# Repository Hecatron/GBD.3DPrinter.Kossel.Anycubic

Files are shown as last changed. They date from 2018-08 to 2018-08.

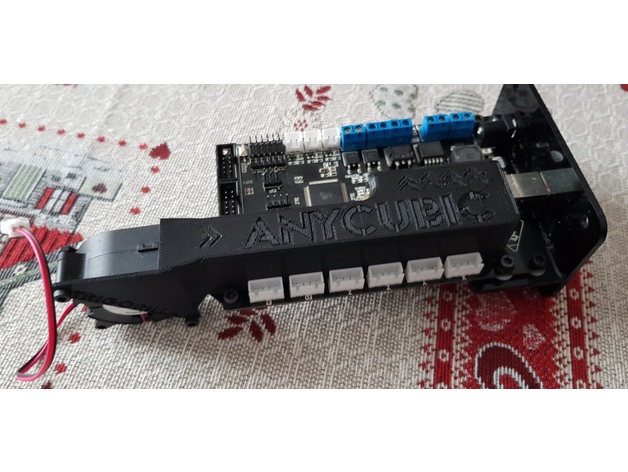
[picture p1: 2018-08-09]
Parts/Upgrades/1/Anycubic_Kossel_Essentials_Part_2_REMIX/files/Anycubic_Trigorilla_Turbo_Fan_Board_Cooler/images/2af14a65b911a9475e456cf5a4f66519_preview_featured.jpg

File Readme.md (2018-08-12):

# Readme

## TODO

Look into getting one of these displays for the Rpi

  * https://www.adafruit.com/product/3578

Also

  * https://www.thingiverse.com/thing:2859992
  * https://www.thingiverse.com/thing:2789305
  * https://www.thingiverse.com/thing:2783047

  * https://www.thingiverse.com/thing:2316500

  * https://www.thingiverse.com/thing:2024677

  * http://www.anycubic3d.com/model/show/1164.html

  * http://www.anycubic3d.com/model/show/1238.html

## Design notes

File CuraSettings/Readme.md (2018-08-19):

# Readme

Backup of settings for my Anycubic Linear Kossel Plus

Typically these settings live under
```
C:\Users\ric\AppData\Roaming\cura\3.4
```

  * Marlin-Cura-3.4 - settings I used with the original marlin / trigorilla control board
  * Duet-Cura-3.4 - settings I used for the new duet wifi control board

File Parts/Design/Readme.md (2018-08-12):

# Readme

Original frame design based on

  * https://www.thingiverse.com/thing:2965780

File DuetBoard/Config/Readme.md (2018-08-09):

# Duet Board Configuration

## Overview

  * https://configurator.reprapfirmware.org/
  * https://betrue3d.dk/duet-wifi-generating-firmware-using-configurator/

## Board Configuration Files

  * config.g – Primary configuration file, where the core configs are stored.

  * bed.g - autoleveling for Delta printers.
  * deployprobe.g - for deploying a probe for Delta printers – Removing this.
  * homedelta.g - homing on a Delta printers.
  * pause.g - for pausing the printer.
  * rResume.g - Resume file.
  * retractprobe.g - to retract a probe.

## Firmware Files

  * DuetWebControl.bin – Web Interface firmware file.
  * DuetWiFiServer.bin – WiFi Server firmware file.
  * iap4e.bin – Electronics firmware file.

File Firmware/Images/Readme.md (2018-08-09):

# Readme

Reference of pinout for trigorilla board

  * anycubic_i3_mega_trigorilla_board.jpg
  * https://drucktipps3d.de/forum/topic/anycubic-i3-mega-trigorilla-board-pin-belegung/

Images of different probes

  * Version1Probe.jpg (this is the one I have)
  * Version2Probe.jpg

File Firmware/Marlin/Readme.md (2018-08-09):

# Readme

## Overview

This is a custom firmware I've come up with for the Anycublic Kossel Linear Plus.
This is the one with the linear guides.

Also I'm using Version 1 of the Probe
As near as I can tell there were two different probes shipped with the Anycublic Kossel Linear Plus.
which uses the probe for autoleveling the bed.

  * Version 1 - has a Z offset of -19.00 below the extruder (this is the one I'm using)
  * Version 2 - has a Z offset of -14.90 below the extruder

It's possible to build your own firmware from the patches I've provided here.
These patches are against Marlin 1.1.8. See the docs directory for information on building the sources.

## Upgrading

### Backup existing firmware

First we want to backup the existing firmware just to be safe
```
avrdude -p atmega2560 -c stk500v2 -P /dev/ttyUSB0 -b 115200 -U flash:r:flash_backup_file.hex
avrdude -p atmega2560  -c stk500v2 -P /dev/ttyUSB0 -b 115200 -U eeprom:r:eeprom_backup_file.hex
```

### Upload new firmware

To overwrite / update the firmware to the one in this repository
see the file \bin\Gbd-Marlin-ProbeV1\Gbd-Marlin.ino.mega.hex
```
avrdude -p atmega2560  -c stk500v2 -P /dev/ttyUSB0 -b 115200 -e -U flash:w:Gbd-Marlin.ino.mega.hex
```

### Reset Settings

To reset the settings to all default settings
and to store them in EEPROM

  * Select Control -> Restore Failsafe
  * Select Control -> Store Settings

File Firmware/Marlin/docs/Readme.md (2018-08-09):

# Readme

This is a collection of code diffs / hex files and notes
I've collected in an attept to update the firmware on my Anycubic Kossel Delta Linear Plus
from the stock firmware which appears to be 1.1.0Rc8 to 1.1.8

## Diffs

### Diffs/Anycubic-1.1.0-rc8.patch

This is a list of differences between stock 1.1.0-RC8 and the Anycubic Sources.
In order to figure out what changes they made to configure it for Marlin.
Note this is from the Anycubic website, but I'm not entirley sure it's the same as the firmware that came with the device
I think the position of the Probe isn't setup so these sources may have been for the one without the probe.

There's also some code in there that's no longer needed for 1.1.8 which turns the fan on when the extruder gets hotter than 60 degrees
Marlin now has a proper way to do this via configuration

### Diffs/namsugak-1.1.8.patch

List of differences in a firmware updated to 1.1.8 by namsugak
It has some stuff in for LED's I'm not using, but I'm using this to check my own configuration settings for 1.1.8

### Diffs/Gbd-1.1.8.patch

TODO
Add in my own patched sources diff / Hex files

## Hex Files

### Bin/OriginalFirmware/

TODO

### Bin/Gbd-Marlin-Base/

TODO

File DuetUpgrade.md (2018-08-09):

# Duet Upgrade

## Controller Board

  * Duet WIFI

## Stepper Motors

  * https://duet3d.dozuki.com/Wiki/Choosing_and_connecting_stepper_motors
  * https://forum.duet3d.com/topic/103/choosing-0-9-degree-steppers
  * 0.9 degree
  * Nema 17
  * around 3A ?

## PSU

  * 24V Power Supply Needed
  * Current?

## Heater Block / Thermistor

Look into the best heater / thermistor using 24V

## Sensor

Look into 6 - 36V sensor

https://www.amazon.co.uk/Leveling-Self-Leveling-Adjustment-Inductive-Proximity/dp/B078K827XL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

## Connectors

### Original Connectors

The trigorrila board uses a combination of

  * 4pin JST-XH connectors - Stepper Motors
  * 2pin JST-XH connectors - Fans
  * 2pin header connectors - End Stops / thermistors
  * http://fi.eurorc.com/files/content_images/Buyers-Guide-OCo-aBalancer-Harness-4.jpg

The duet board uses Molex KK type connectors

  * 22-01-2045 - 4pin - Stepper Motors
  * 22-01-2035 - 3pin - End Stops
  * 22-01-2025 - 2pin - Thermistors and Fans
  * https://duet3d.dozuki.com/Wiki/Connector_and_spare_part_numbers

### Stepper Motor Connectors

The stepper motors use 6pin JST-XH connectors
The best plan is to get some leads with these on the end, then replace the header connectors with the Molex ones used by the Duet board

  * https://www.amazon.co.uk/BESTOMZ-Bipolar-Stepper-Printers-Machines/dp/B0746GJ7BR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

### Fan Connectors

  * https://www.amazon.co.uk/dp/B01GZKFML0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

### End Stop Connectors

TODO

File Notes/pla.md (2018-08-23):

1. printing at a higher temp such as 205 doesn't give as much adhesion as 190
so it's best to print the first layer at 190, then the follow on layer at 205 for a shiny surface finish

2. a bed temp of 50 is needed to avoid warping
a higher bed temp like 70 will stick more, but the lower layers won't cool quickly enough
which will result in the middle layers cooling before the lower ones
and a major warpage

3. general overrides

initial layer speed 5
printing temperature initial layer 190
initial layer height 0.1

4. with pla generally more fan is better for finer detail
however it can reduce bed adhesion so it's best to enable only after around 0.5mm or 6 layers

TODO try experimenting with 100% / 75%

5. rounded corners seem to be a big plus to avoid lifting as well on parts
although with a cooler bed at 50 it shouldn't be a problem

6. when leveling the bed / doing auto calibration
leave the bed at 60 for a long while to allow the heat to spread out / even out the bed
if a brim lifts at one corner this suggests the head is too far away at that corner

7. one technique I've found for bed adeshion is the initial layer height setting
at 0.1 the minimum this is good for calibrating the delta height of the printer
at a higher value the head is lifted up and more plastic is extruded to give a thicker initial layer
this sticks to the bed a lot better
however this seems to cause wrippling in the bottom surface layer
0.3 = default
0.2 = might be best

TODO try experimenting with 0.2 then baby step down by 0.05 to smoosh it into the bed

8. another technique to get better bed sticksion is to use a initial line width of 115%
https://www.sd3d.com/pla-settings/

In short

  * set the initial printing temp to 190 for the first layer, then something higher if wanted for the default for a shiny surface finish
  * use 0.1 for the initial layer height, avoid anything higher as it tends to cause wrippling - TODO
  * instead use 115% for the initial line width to help with adhesion, better alternative to large initial line height
  * use max 75% fan speed with 3 duct fan, and only full on after 0.5mm / 6 layers to help avoid warping
  * use a bed temp of 50 to avoid warping (this is a big one)
  * try to avoid non rounded corners in the model if warping is a problem

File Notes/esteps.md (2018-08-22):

M92 X80 Y80 Z80 E96                                  ; Set steps per mm
1. Measure 200mm, and put a bit of tape on
2. extrude 190mm
3. measure the amount left
4. e.g. 12mm left when it should be 10 means only 188mm has been extruded

(What you asked for / What you actually got) * current E-steps.
190 / 185 * 96 = 98.6 (new steps value)

M92 X80 Y80 Z80 E98.6                                  ; Set steps per mm

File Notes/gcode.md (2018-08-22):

Under the duet we're currently getting
"M205 command is not supported"
from the G-code output from cura

  * http://marlinfw.org/docs/gcode/M205.html

This seems to be a setting for the acceleration / speed etc

according to this

  * https://duet3d.dozuki.com/Wiki/G-Codes_not_implemented

we should be using M566 instead

TODO check different outputs from cura

gcode output changed from Marlin to Reprap
check if this works

also
https://github.com/fieldOfView/ZOffsetPlugin

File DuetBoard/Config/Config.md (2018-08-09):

# Config

## General

### General Preferences

  * Board:  Duet 2 WIFI (default)
  * Firmware version: 1.21 or newer (default)
  * Firmware compatibility: Marlin
  * Enable non-volatile memory: unchecked
    I think this isnt needed since settings are read from the sd card on startup anyway
    so we dont need g-codes loaded from the eeprom
  * Save print state on power failure: ticked
  * Auto save threshold: 10 Volts (if the psu drops below this voltage)
  * Resume threshold: 11 Volts

### Printer Geometry

  * Delta Geometry
  * Printable radius: 116.0 mm
  * Minimum Z: 0 mm
  * Diagonal rod length: 271.5 mm
  * Homed height: 295.2 mm // Auto calibrate
  * Maximum carriage travel: // I thnk not used for delta, specifed 300

  * Add a warning in config.g if you are setting your homed height too high and will measure it during calibration: ticked

#### Delta Radius

  * Smooth rod offset - 186 mm
  * effector offset - 31 mm
  * carriage offset - 20.6 mm
  * radius = 186 - 31 - 20.6
  * radius: 134.4 // Auto calibrate

## Motors

### Axes

  * Direction: Forwards - TODO test
  * Microstepping: x16 interpolate
  * Max. instant speed change: 5
    This is the jerk speed under marlin
  * Max speed: 200
  * Acceleration: 2000
  * Motor current: 1200
    motor is nema17 / 40mm deep, typically these are rated at 1.5A, so 85% of that is approx 1.2A
    The figure you put in config.g is the peak current per phase

#### Steps per mm

  * Full steps per rotation: 200
  * Belt pitch: 2
  * Pulley teeth: 20
  * Motor Steps per mm: 200 * 16 / 2 / 20
  * Motor Steps per mm: 80

### Extruders

  * Number of extruders: 1

  * Direction: Forwards - TODO test
  * Microstepping: x16 interpolate
  * Max. instant speed change: 5
  * Max speed: 50
  * Acceleration: 2000
  * Motor current: 1200

#### Steps per mm

  * Motor Steps per mm: 96
    (originally 96 in marlin)

### Motor current reduction

  * Reduce motor currents automatically when idle: ticked (default)
  * Idle current percentage: 30% (default)
  * Idle timeout: 30s (default)

## Endstops

### Z-Probe

  * Probe X Offset: 0
  * Probe Y Offset: 0
  * Probing speed: 2
    TODO I think marlin is set to 1000
  * Mode: 4
  * Deploy / retract probe (unticked)
  * Trigger Height: +16.8 // requires manual calibration
  * Trigger Value: 100 (default)
  * Recovery time: 0.4 (default)

### Endstop configuration

Endstop Type

  * X - Active High / Normally Closed
  * Y - Active High / Normally Closed
  * Z - Active High / Normally Closed

### Homing preferences

TODO

  * Homing speed (first pass): 30 (default)
  * Homing speed (second pass): 6 (default)
  * Travel speed: 100 (default)
  * Z dive height: 5 (default)

tick the box under "Set initial homing speed to 10% for calibration and add a note to homedelta.g "

## Heaters

### General heater settings

  * Number of nozel heaters: 1
  * Assign bed heater to first nozzle: unticked (default)
  * Heated bed present: ticked (default)
  * Bed heater output: Bed (default)
  * Control Method: PID // TODO selected bang bang for now
  * Chamber heater present: unticked (default)

### Heaters

For both the bed and the hotend
In marlin the thermistor setting is 5
this is labled as - 100K thermistor - ATC Semitec 104GT-2/104NT-4-R025H42G (Used in ParCan & J-Head) (4.7k pullup)
in thermistortables.h this maps to thermistortable_5.h

I think we can fine tune the B / C values using a digital thermometer

Bed

  * Temp limit: 120
  * PMW limit: 100
  * Series res: 4700 // Resistor on the controller board that is in series (correct value for duet wifi)
  * R25: 100000 // 100K at 25C temperature
  * B: 4267
  * C: 0

E0

  * Temp limit: 275
  * PMW limit: 100
  * Series res: 4700 // Resistor on the controller board that is in series (correct value for duet wifi)
  * R25: 100000 // 100K at 25C temperature
  * B: 4267
  * C: 0

## Tools

### Tool mapping

  * Number of tools: 1
  * Wait for temperatures to be reached on tool change: ticked
  * Select first tool on start-up: ticked
  * all offsets: 0mm

## Compensation

### Delta calibration

  * Number of peripheral points: 10
  * Number of halfway points: 6
  * Number of calibration factors: 7
  * Probing radius: 110

### Grid compensation

  * Probing radius: 110
  * Spacing between probe points: 25 (default)

### Orthogonal axis compensation

TODO - leave unticked for now

## Network

### Network settings 

  * Printer name: Anycubic1
  * Enable network: ticked (default)
  * Aquire dynamic IP address via DHCP: ticked (default)
  * Enable Http: ticked (default)
  * Enable FTP: unticked (default)
  * Enable Telnet: unticked (default)

  * WIFI access point name: *****
  * Password: *****
  * WIFI Password: *****

## Finish

### Cooling fans

  * Confirmed that the fans are 12V

FAN0

  * Name: Part Fan
  * Value 100%
  * Invert output: No
  * Frequency: 31Hz
  * Thermostatic Control: No

FAN1

  * Name: Hotend Fan
  * Value 100%
  * Invert output: No
  * Frequency: 31Hz
  * Thermostatic Control: Yes
  * Monitored Heaters: E0
  * Trigger temperature: 60

FAN2

  * Name: Controller Fan
  * Value 100%
  * Invert output: No
  * Frequency: 31Hz
  * Thermostatic Control: No

### Miscellaneous

  * Custom G Codes / non required

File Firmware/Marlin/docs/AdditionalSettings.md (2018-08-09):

# Additional Settings

## Overview

This is a list of changes I think are different from the original Stock firmware
That I've included in my own version of the firmware

namsugak's firmware has G26_MESH_VALIDATION disabled, I've left this enabled

## Configuration.h

### Delta AutoCalibration

Delta Auto Calibration is enabled

  #define DELTA_AUTO_CALIBRATION
  #define DELTA_CALIBRATION_RADIUS 93.0 // Default 100.8mm

### Slower feedrate for homing

The feedrate for homing has been slowed down a bit
  #define HOMING_FEEDRATE_Z  (50*60)

### Slow Probe Speed

The probing speed has been slowed down from /2 to /3
  #define Z_PROBE_SPEED_SLOW (Z_PROBE_SPEED_FAST / 3)

### Delta Probable Radius

Delta probable radius changed from -30 to -10 
  #define DELTA_PROBEABLE_RADIUS (DELTA_PRINTABLE_RADIUS - 10)

### Unified Bed Leveling

These settings where taken from namsugak's firmware settings
  #define _PX(R,A) (R) * cos(RADIANS(A))
  #define _PY(R,A) (R) * sin(RADIANS(A))
  #define UBL_PROBE_PT_1_X _PX(DELTA_PROBEABLE_RADIUS, 0)   // Probing points for 3-Point leveling of the mesh
  #define UBL_PROBE_PT_1_Y _PY(DELTA_PROBEABLE_RADIUS, 0)
  #define UBL_PROBE_PT_2_X _PX(DELTA_PROBEABLE_RADIUS, 120)
  #define UBL_PROBE_PT_2_Y _PY(DELTA_PROBEABLE_RADIUS, 120)
  #define UBL_PROBE_PT_3_X _PX(DELTA_PROBEABLE_RADIUS, 240)
  #define UBL_PROBE_PT_3_Y _PY(DELTA_PROBEABLE_RADIUS, 240)

### Grid Max points

The default setting for this is 3, Anycubic stock uses 5, I've set it to 9
  #define GRID_MAX_POINTS_X 9

### Maximum Feedrate

THe max feedrate for the Extruder is lowered from 200 to 50
  #define DEFAULT_MAX_FEEDRATE          { 200, 200, 200, 50 }

### Fixed Probe

Indicates the probe is fixed
  #define FIX_MOUNTED_PROBE

### PID Autotune

Add PID Autotune to the LCD "Temperature" menu to run M303 and apply the result.
  #define PID_AUTOTUNE_MENU

### Print Counter

This allows pulling back information on the number of prints etc via M78
  #define PRINTCOUNTER

### Nozzel Park

Specify a position for the Nozzel parking position
  #define NOZZLE_PARK_FEATURE
  #define NOZZLE_PARK_POINT { (X_MIN_POS + 10), (Y_MAX_POS - 10), 30 }
  #define NOZZLE_PARK_Z_FEEDRATE 100     // Z axis feedrate in mm/s (not used for delta printers)

### No motion before homing

This should hopfully avoid crashes into the bed
  #define NO_MOTION_BEFORE_HOMING  // Inhibit movement until all axes have been homed

## Configuration_adv.h

### Case Fan

This should allow the use the unpopulated fan header 1
for a cooling fan for the main trigorilla board
  #define USE_CONTROLLER_FAN
  #define CONTROLLER_FAN_PIN 7

### Part Cooling Fan Kick

I've noticed when running the part cooling fan at low speeds it sometimes needs a kick to get it going
This should fix that
  #define FAN_KICKSTART_TIME 100

### Advanced Pause

This should enable the advanced pause feature
  #define ADVANCED_PAUSE_FEATURE
  #define FILAMENT_CHANGE_UNLOAD_FEEDRATE 25
  #define FILAMENT_CHANGE_LOAD_LENGTH 50
  #define ADVANCED_PAUSE_EXTRUDE_LENGTH 30
  #define PAUSE_PARK_NOZZLE_TIMEOUT 600
  #define PARK_HEAD_ON_PAUSE

### Z safe homing

I think this is safe to enable
it recommends switching on for probing / auto leveling
  #define Z_SAFE_HOMING

## TODO

### Leveling Fade Height

  This seems to be disabled in one of the firmware's I've come across
  for now I'm leaving it enabled
  TODO try measuring the height of a part, if it's too high / large then try disabling

  #define ENABLE_LEVELING_FADE_HEIGHT

### Alternative auto leveling

UBL Bed leveling seems to have more features and is more detailed
but I think it has issues on non square beds, in that sense Bilinear seems to be more reliable at least with 1.1.8

I need to retry AUTO_BED_LEVELING_UBL with 1.1.x bugfix branch which has more fixes

### software endstops

try enabling this
MIN_SOFTWARE_ENDSTOPS
MAX_SOFTWARE_ENDSTOPS

### Probe Z-offset

this seems to have wrecked my probe

MSG_DELTA_Z_OFFSET_CALIBRATE
Probe Z-offset

G33 P-1

after May 12
before May 15

### Bed Leveling

so far G33 seems to do a pretty good job of getting the bed level
but using the spiral calibration, it looks like there's some regions towards the outside of the plate
which are raised / too close to the nozzel (high points)

these might be caused by the existing plate brackets, so some new ones may get around this

  * try enabling / setting up bi-linear autoleveling next and switch it on to see if it compensates
  * try replacing the bed brackets with some different ones (needs to account for the ultrabase)
  * when printing the spiral reduce the scale to 95%

DELTA_CALIBRATION_RADIUS set to 110mm about 6mm short of the printable radius
also the bed wasn't properly seated.

### Diagaonal Rod

We can tweak this value to alter the scale of the print

  * The larger this value, the smaller in scale the part becomes
  * The smaller this value, the larger in scale the part becomes

### EStep Tuning

Remember to tune the E Steps for the amount of filament extruded
(tape on filament, measure out 50mm etc)

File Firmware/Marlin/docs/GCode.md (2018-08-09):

# G-Code Commands

## Firmware Info

To get the current version of the firmware use the command M115

The output of the default firmware included with the printer is
```
FIRMWARE_NAME:Marlin 1.1.0Anycubic SOURCE_CODE_URL: PROTOCOL_VERSION:1.0 MACHINE_TYPE:Anycubic EXTRUDER_COUNT:1 UUID:cede2a2f-41a2-4748-9b12-c55c62f367ff
```

## Get Autoleveling settings

### Zero Bed

Select Measure Zero Pos seems to run the following commands

  * G36 - shortcut to the below commands

  * G28 - Auto Home
  * G29 - Auto Bed Leveling - http://marlinfw.org/docs/gcode/G029-abl.html
  * G28 - Auto Home
  * M888 - Check bed Leveling? - seems to reset the printer

### Level Bed

  * G35 - shortcut to the below commands

  * G28 - Auto Home
  * G29 - Auto Bed Leveling - http://marlinfw.org/docs/gcode/G029-abl.html
  * G28 - Auto Home
  * G30 - Do a single Z probe at a specified position. By default probe in the current position.

### General List

  * G28 - Auto Home
  * G29 - Auto Bed Leveling - http://marlinfw.org/docs/gcode/G029-abl.html
  * G30 - Do a single Z probe at a specified position. By default probe in the current position.
  * M888 - reset machine?

  * M48 - This isn't on the menu, but tests the Z probe by sampling the same spot multiple times
  * M501 - I think can read the EEPROM settings

  * G33 ? delta auto calibration?
  * http://marlinfw.org/docs/features/auto_bed_leveling.html

### Probe test

  * M119 - I think we can use this to test the Z Probe (if it should be inverted)
  to invert the probe we need to change the below settings (default it true)
  Z_MIN_ENDSTOP_INVERTING
  Z_MIN_PROBE_ENDSTOP_INVERTING

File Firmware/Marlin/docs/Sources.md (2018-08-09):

# Sources

## Base Marlin Source

### Default Marlin

 we can download the default marlin firmware for 1.1.8 - Dec 25, 2017 from here
 (unconfigured)

  * https://github.com/MarlinFirmware/Marlin/tree/1.1.8

### Bugfix 1.1.x

The latest devel version is 1.1.x, this also has a patch in for trigorilla board support

  * https://github.com/MarlinFirmware/Marlin/pull/8367
  * https://github.com/MarlinFirmware/Marlin/tree/bugfix-1.1.x

### Arduino Libraries

We may need the following arduino libs installed

  * https://github.com/olikraus/U8glib_Arduino \\
    For a full graphics display

## Stock Firmware

  * http://www.anycubic3d.com/support/show/594034.html
  * https://www.thingiverse.com/thing:2220077

There seems to be around 3 different versions of the firmware available from the official site

  * Kossel Plus_20170712
    This seems to be a source based distro, I think the same version included with the printer Marlin 1.1.0-RC8 - 6 Dec 2016
    TODO is autoleveling enabled?
 
  * ANYCUBICkossel Auto leveling_20171113 (version 1 / version 2)
    This includes two binary based hex files (no source) also appears to be Marlin 1.1.0
    It looks like there's 2 different versions of the probe so they've included 2 versions and a picture to match against the probe
    My probe appears to be V1, I suspect the V2 probe has a different height measurement.

In order to work out what custom settings have been applied we can compare it to version 1.1.0-RC8

  * https://github.com/MarlinFirmware/Marlin/tree/1.1.0-RC8

see Diffs/Anycubic-1.1.0-rc8.patch

## Other Firmwares

### namsugak firmware

This appears to have Neopixel support and is based on 1.1.8
however it's setup for the V2 sensor, I think mine is V1

  * https://www.thingiverse.com/thing:2803527

### ArtieH firmware

This one is more recent, it's based on the 1.1.x bugfix branch
this seems to be more of a dev version

  * https://www.thingiverse.com/thing:2927795

### Another firmware

  * https://github.com/ruevs/Marlin_Anycubic_Kossel

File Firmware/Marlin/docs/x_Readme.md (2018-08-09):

# Readme

## Overview

This directory contains some hex binary files for different Marlin versions

  * **OriginalFirmware** - A backup of the version of Marlin that came with my Anycubic Kossel Linear Plus <br>
    This has version 1 of the probe as far as I can tell, and is Marlin 1.1.8RC8

  * **Gbd-Marlin-Base** - My own version of Marlin 1.1.8, no modifications other than trying to update from 1.1.0-RC8 to 1.1.8

When compiling using the Arduino Software

  * select the board Tools -> Board -> Arduino Genuino Mega or Mega 2560
  * select Verify / Compile
  * select Sketch -> Export Compiled Binary
  * the hex file (use the one without the bootloader) will be in the Marlin Source directory

## AVRDude commands

### Backup existing firmware

  * https://forum.arduino.cc/index.php?topic=403201.0

To backup the main firmware, reset the device then run
```
avrdude -p atmega2560 -c stk500v2 -P /dev/ttyUSB0 -b 115200 -U flash:r:flash_backup_file.hex
```

To backup the eeprom reset the device
make sure octoprint is disconnected
then run
```
avrdude -p atmega2560  -c stk500v2 -P /dev/ttyUSB0 -b 115200 -U eeprom:r:eeprom_backup_file.hex
```

### Write new firmware

To write a hex file
```
avrdude -p atmega2560  -c stk500v2 -P /dev/ttyUSB0 -b 115200 -e -U flash:w:flash_backup_file.hex
```

To write a backed up eeprom
```
avrdude -p atmega2560  -c stk500v2 -P /dev/ttyUSB0 -b 115200 -U eeprom:w:eeprom_backup_file.hex
```

### Hex to Bin conversion

to convert binary to hex
```
srec_cat.exe BinFile.bin -Binary -o HexFile.hex -Intel
```
to convert hex to binary
```
srec_cat.exe HexFile.hex -Intel -o BinFile.bin -Binary
```

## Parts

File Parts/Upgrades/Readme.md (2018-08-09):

# Readme

Collection of upgrades, some sourced from thingiverse <br>
for an anycubic linear plus (one with rails)

  * https://www.thingiverse.com/tag:Anycubic_Kossel_Plus/

## Custom Upgrades

### Camera Mount

A couple of parts for mounting a camera on the 3d printer - Advent AWCAMHD15

### Rpicase-Lasercut

Designs for a laser cut case for a Rpi to mount on the printer.
The printer version includes M4 mounting holes for the 20x20 extrusion

### LargeDisplayMount

Panel to mount a larger LCD display on the front of the printer <br>
KOOKYE LCD 12864 Graphic Smart Display Controller Module with Connector Adapter & Cable for RepRap RAMPS 1.4 3D Printer kit Arduino Mega 2560 R3 Shield

  * https://www.amazon.co.uk/gp/product/B019SXNH1S/

Look into

  * https://www.thingiverse.com/thing:2911892
  * https://www.thingiverse.com/thing:2489092

## Thingiverse Upgrades

### ExtruderClip

Can be used when changing filaments

  * https://www.thingiverse.com/thing:2935798

### Flexible filament holder

  * https://www.thingiverse.com/thing:2788235

### Cable Holder

  * https://www.thingiverse.com/thing:2897799

### Bottom Cover

This one has ventalation holes and mounting holes for M4 bots

  * https://www.thingiverse.com/thing:2771991

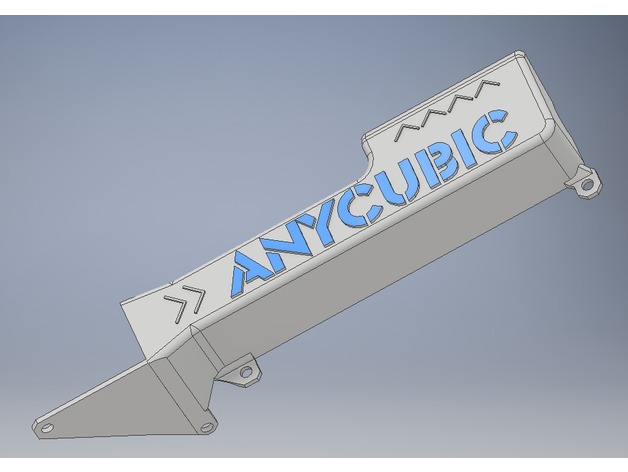
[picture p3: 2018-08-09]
Parts/Upgrades/1/Anycubic_Kossel_Essentials_Part_2_REMIX/files/Anycubic_Trigorilla_Turbo_Fan_Board_Cooler/images/becb625ca1ba965f619c9286a48681f2_preview_featured.jpg

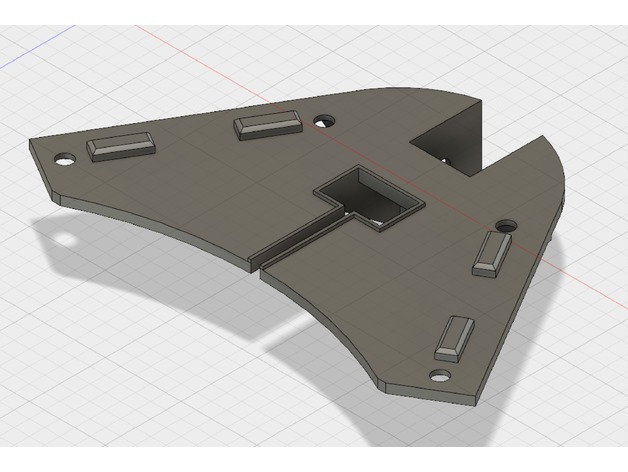
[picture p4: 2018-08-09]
Parts/Upgrades/1/Anycubic_Kossel_Essentials_Part_2_REMIX/files/Kossel_Plus_Boden_Platte_Kossel_Plus_Bottom_Plate_240mm/images/79d7a0f26c9bd90c7aafae191fd92289_preview_featured.jpg

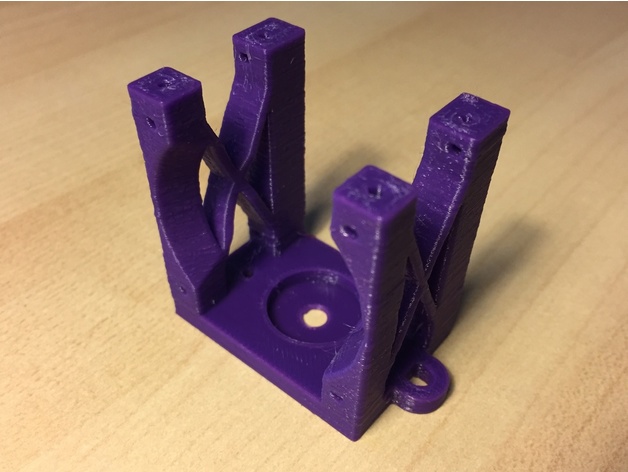
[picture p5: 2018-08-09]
Parts/Upgrades/1/Anycubic_Kossel_Essentials_Part_2_REMIX/files/Anycubic_Kossel_Hotend_Mount_Zesty_Nimble_Mount_Holes/images/835dffdc6f4afb127d733eec75e4aa49_preview_featured.JPG

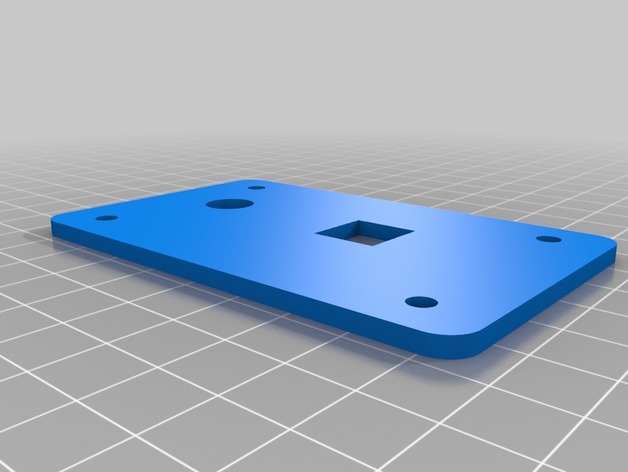
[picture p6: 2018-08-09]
Parts/Upgrades/1/Anycubic_Kossel_Essentials_Part_2_REMIX/files/Anycubic_Kossel_mainboard_cover/images/d7e54eb4350ff4413ee2c9dc20198bfc_preview_featured.jpg

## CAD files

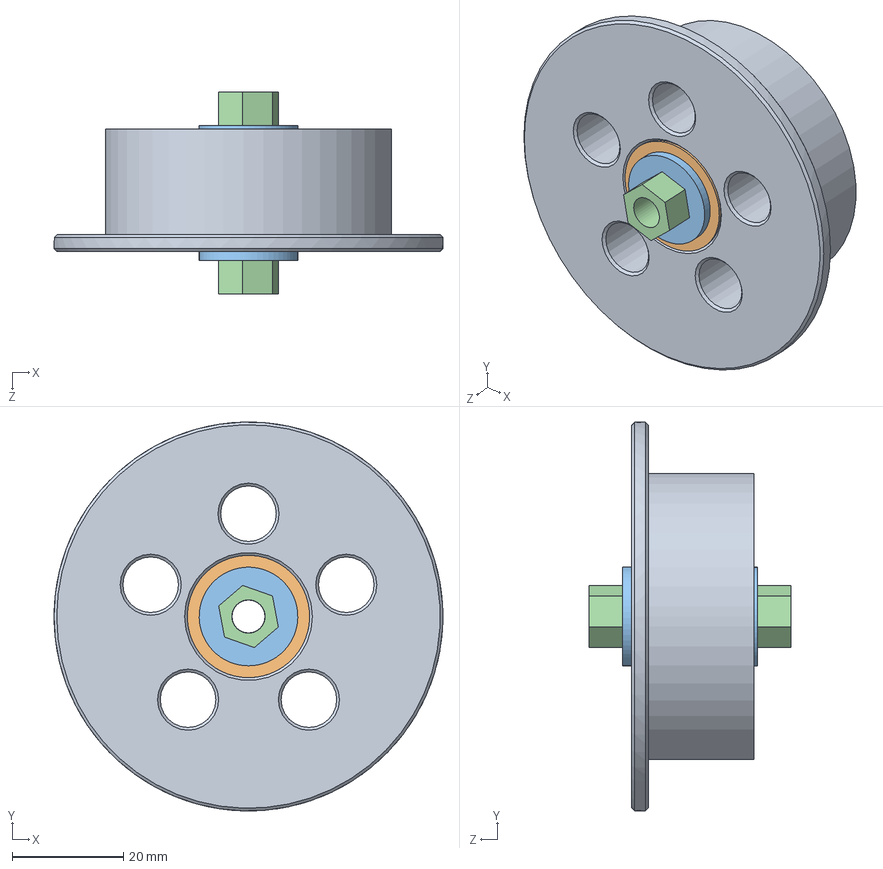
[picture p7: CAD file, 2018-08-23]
Parts/Design/Upgrades/Mine/DualTopMountedSpoolHolder/SpindleAssembly.SLDASM
70.0 x 70.0 x 36.3 mm
Spool_Holder_Spindle
Bearing x 2
M6 Washer x 2
M6 Nut x 2
M6BearingSpacer

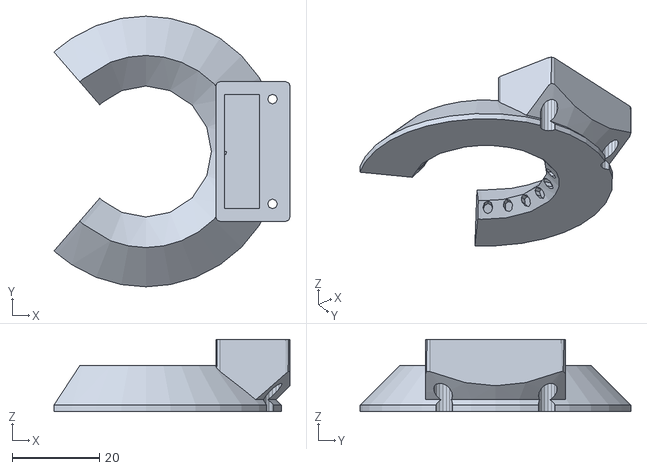
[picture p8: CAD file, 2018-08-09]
Parts/Upgrades/1/Anycubic_Kossel_Essentials_Part_2_REMIX/files/ANYCUBIC_Kossel_Delta_Filament_Cooler_Fan_Duct/files/fan_duct_assembled.stl
54.1 x 62.0 x 16.5

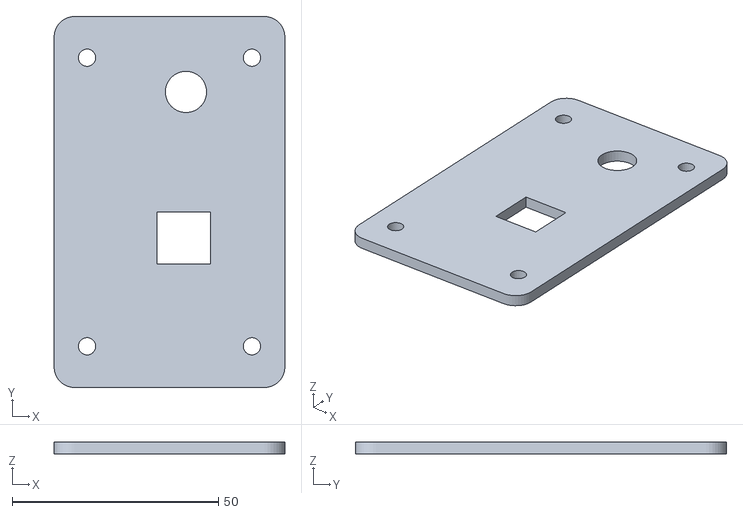
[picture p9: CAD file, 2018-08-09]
Parts/Upgrades/1/Anycubic_Kossel_Essentials_Part_2_REMIX/files/Anycubic_Kossel_mainboard_cover/files/anycubic_mainboard_cover.stl
56.0 x 90.0 x 3.00

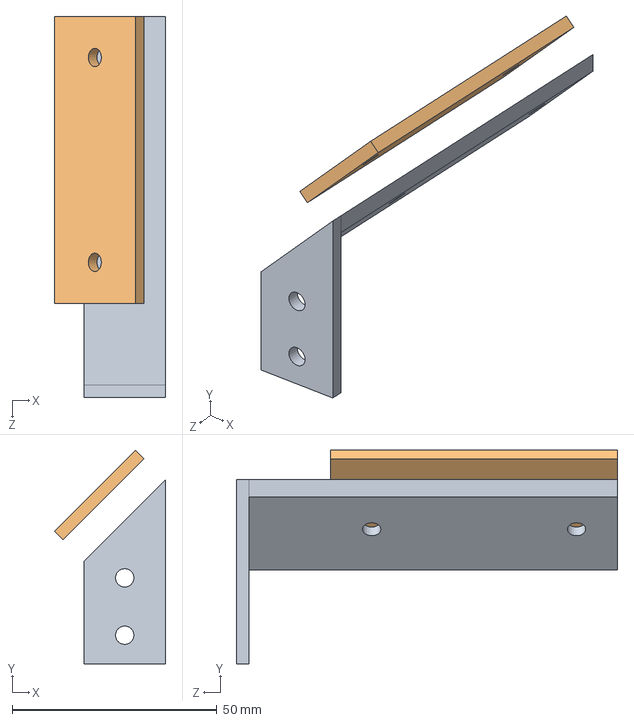
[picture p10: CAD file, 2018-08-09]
Parts/Upgrades/Mine/CameraMount/Root.SLDASM
27.2 x 52.2 x 93.0 mm
CameraMount1
CameraMount2

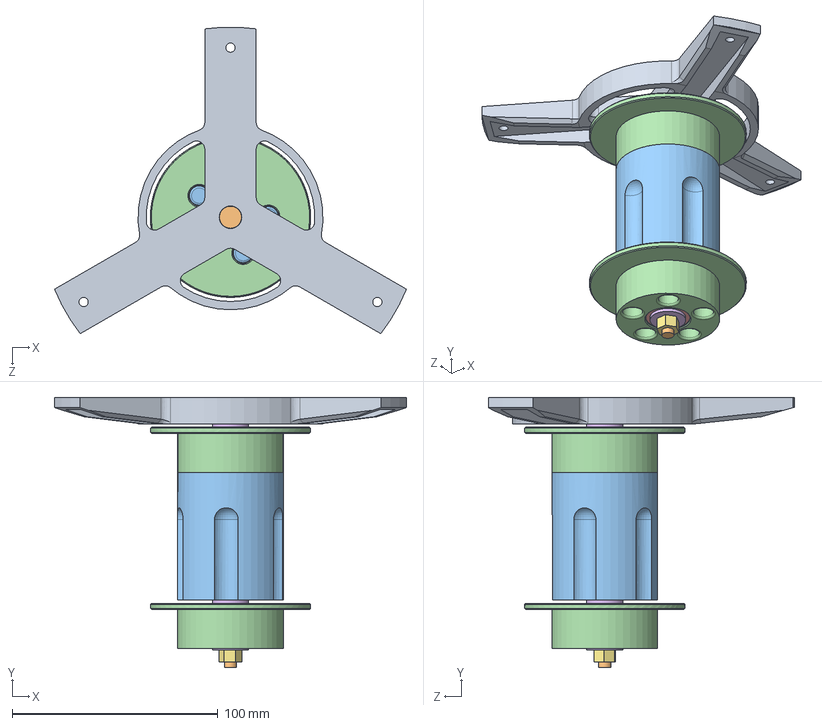
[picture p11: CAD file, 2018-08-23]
Parts/Design/Upgrades/Mine/DualTopMountedSpoolHolder/SpoolAssembly.SLDASM
171.2 x 131.6 x 149.1 mm
Spool_Holder
M6 Bolt x 2
Spacer1
Spool_Holder_Spindle x 2
Bearing x 4
M6 Washer x 4
M6 Nut x 4
M6BearingSpacer x 2

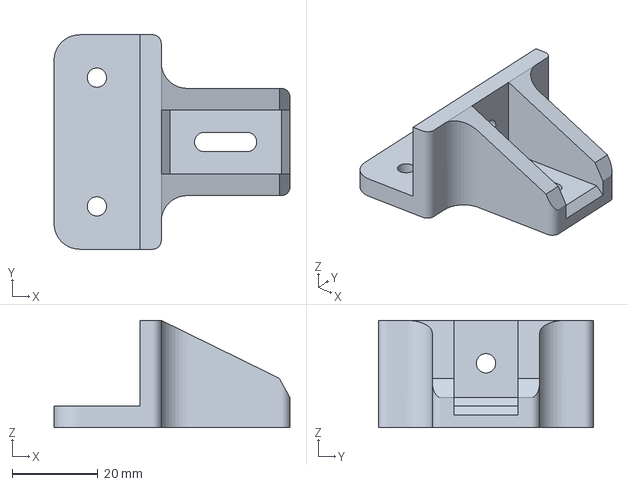
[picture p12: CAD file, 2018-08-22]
Notes/test1.3mf
55.0 x 50.0 x 25.0 mm

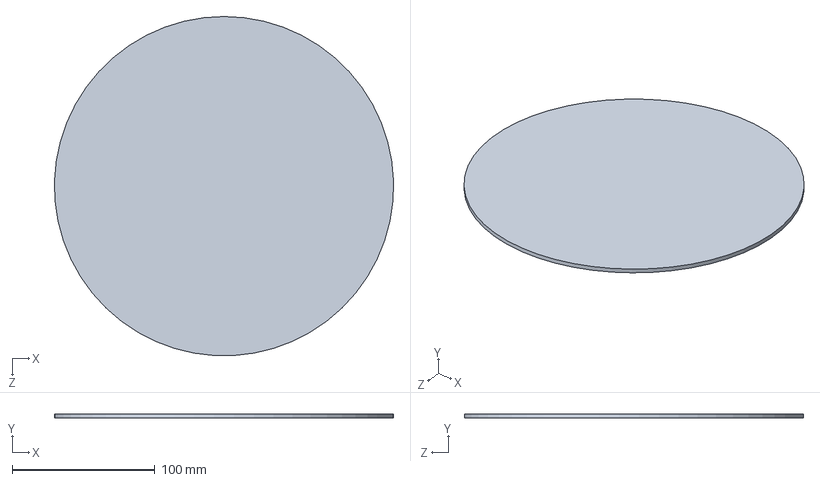
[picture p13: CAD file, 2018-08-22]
Parts/Design/OriginalFrame/Bed/alumium_bed.SLDPRT
237.9 x 3.00 x 237.8 mm

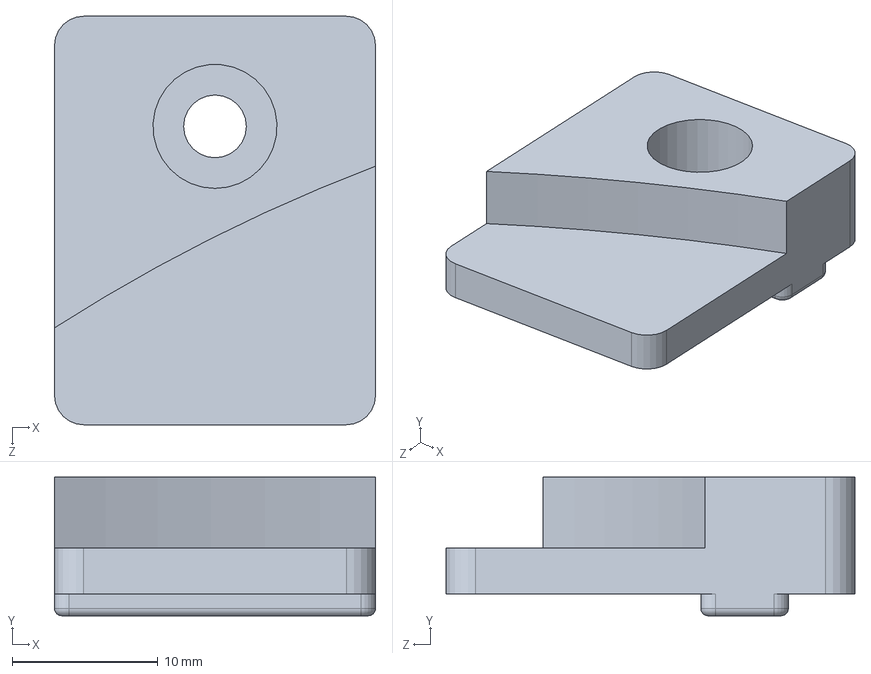
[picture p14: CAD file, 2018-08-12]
Parts/Design/OriginalFrame/BedMountOriginal/bed_mount_mir.SLDPRT
22.0 x 9.50 x 28.0 mm

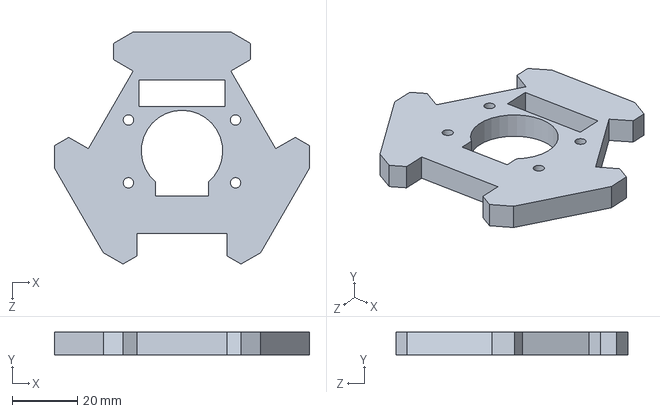
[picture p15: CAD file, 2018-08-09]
Parts/Design/OriginalFrame/Effector/AnycubicEffector.SLDPRT
78.3 x 7.00 x 71.2 mm

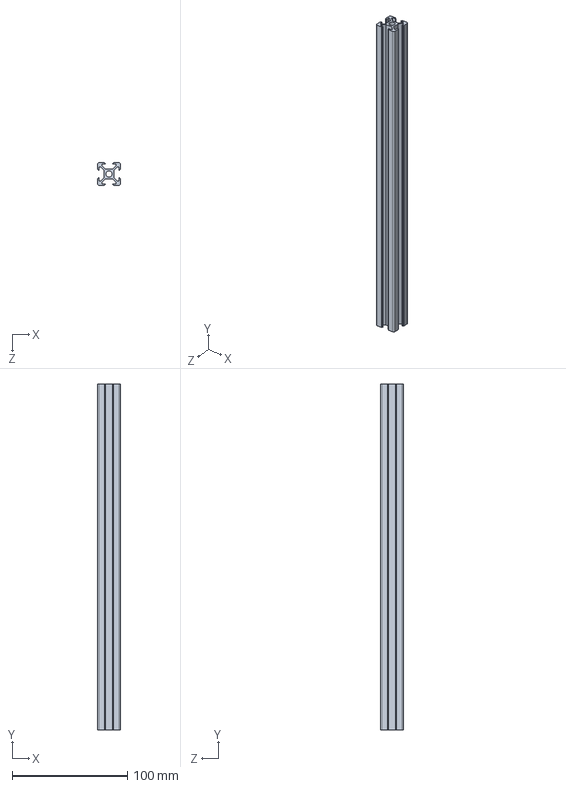
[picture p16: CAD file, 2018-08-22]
Parts/Design/OriginalFrame/Extrusions/printer_aluminum_short.SLDPRT
20.0 x 300.0 x 20.0 mm

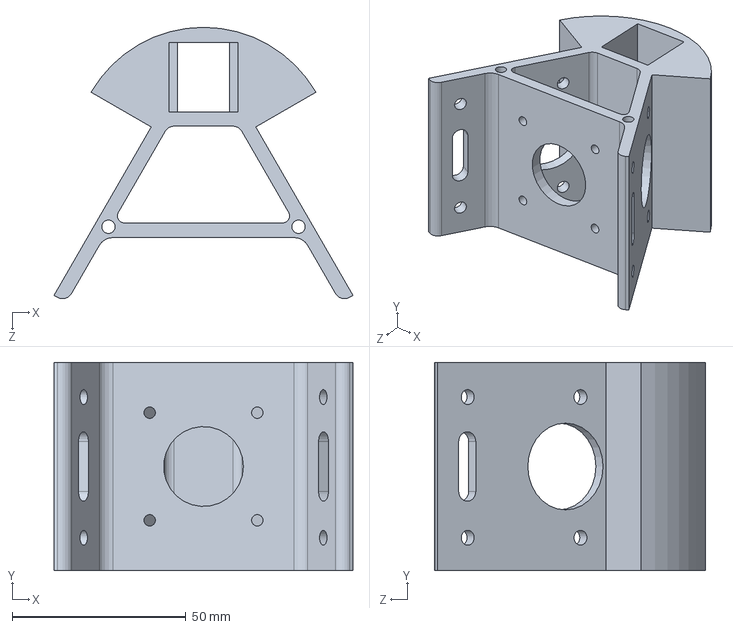
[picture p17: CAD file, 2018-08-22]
Parts/Design/OriginalFrame/FrameBrackets/printer_triangle_piece_long.SLDPRT
86.1 x 60.0 x 78.1 mm

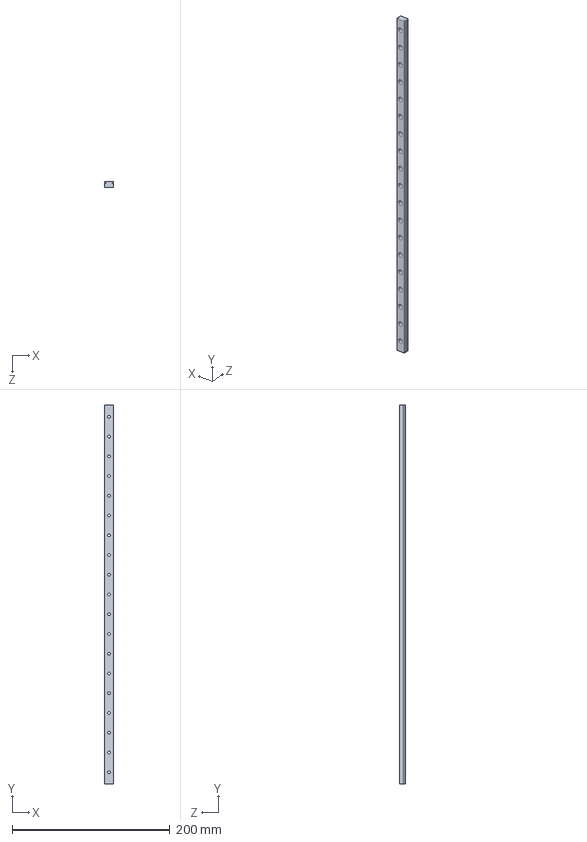
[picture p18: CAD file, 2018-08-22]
Parts/Design/OriginalFrame/LinearRail/linear_rail.SLDPRT
12.0 x 480.0 x 8.00 mm

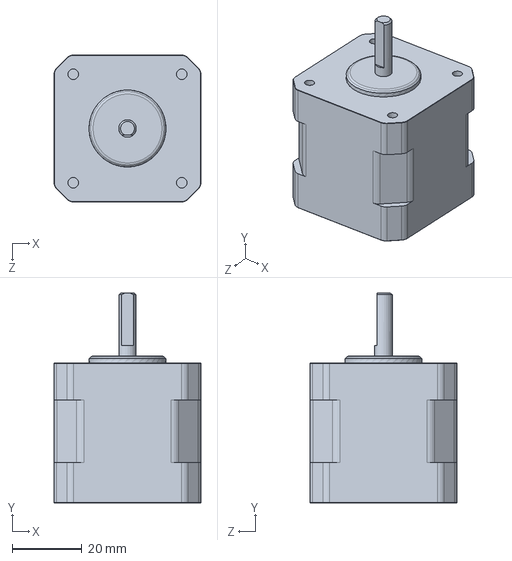
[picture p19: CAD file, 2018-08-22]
Parts/Design/OriginalFrame/Motor/nema_17.SLDPRT
42.0 x 60.0 x 42.0 mm

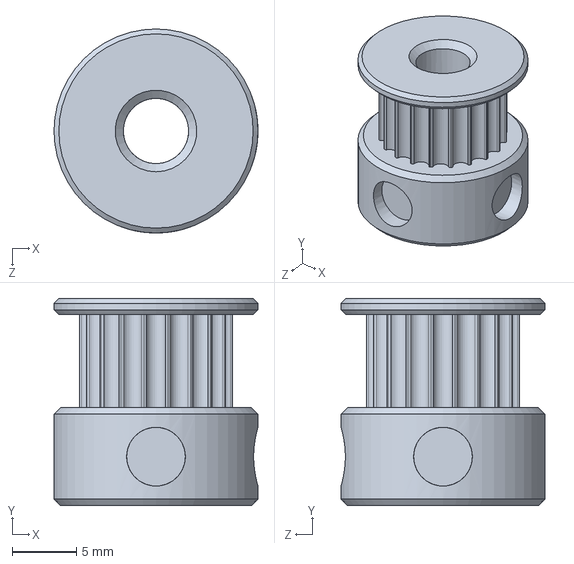
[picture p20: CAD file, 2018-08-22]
Parts/Design/OriginalFrame/Pulleys/20t_pulley.SLDPRT
15.9 x 16.1 x 15.9 mm

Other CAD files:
Parts/Design/Upgrades/Mine/ExtruderTopRailBracket/ExtruderTopRailBracket.SLDPRT
Parts/Design/Upgrades/Mine/Rpicase-Lasercut/Layer3.SLDPRT
Parts/Design/Upgrades/Thingiverse/3WayFanDuct/AnyCubic_Part_Fan_v3.stl
Parts/Design/Upgrades/Thingiverse/BedClips/BedClip.SLDPRT
Notes/ALP_duetwifi_mount_front.3mf
Notes/Anycubic_Plus_Bed_Clip.stl
Parts/Design/OriginalFrame/BedMountOriginal/bed_mount.SLDPRT
Parts/Design/OriginalFrame/Extrusions/printer_aluminum_long.SLDPRT
Parts/Design/OriginalFrame/FrameBrackets/printer_triangle_piece_short.SLDPRT
Parts/Design/OriginalFrame/LinearRail/linear_rail_mount.SLDPRT
Parts/Design/OriginalFrame/Pulleys/20t_idler_pulley.SLDPRT
Parts/Design/Upgrades/Mine/DualTopMountedSpoolHolder/M6BearingSpacer.SLDPRT
Parts/Design/Upgrades/Mine/DualTopMountedSpoolHolder/STL/Spool_Holder_Bracket.STL
Parts/Design/Upgrades/Mine/DualTopMountedSpoolHolder/Spacer1.SLDPRT
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

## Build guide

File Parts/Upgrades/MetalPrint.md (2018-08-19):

# Metal Printing

## Overview / Idea

1. Get some powdered metal
2. put a layer down of 0.1mm / using a roller to flattern
3. raise the roller by 0.1mm each time
4. fix the powder in place using a binder sprayed from a print head

Once part is complete
1. place into a crucible
2. surround with sand
3. place in oven to cure metal

## Links

  * https://www.kickstarter.com/projects/nicholasclewis/inkshield-an-open-source-inkjet-shield-for-arduino/updates
  * https://hackaday.com/2018/03/20/repurposing-inkjet-technology-for-3d-printing/
  * https://www.thingiverse.com/thing:11907

  * https://hackaday.com/2010/12/18/inkjet-print-head-made-with-a-3d-printer/
  * https://reprap.org/wiki/Reprappable-inkjet

  * https://www.thingiverse.com/thing:471235
  * https://www.thingiverse.com/thing:27794
  * http://pwdr.github.io/
  * https://www.youtube.com/watch?v=s8_mo3at40M

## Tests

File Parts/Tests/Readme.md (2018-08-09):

# Test Parts

## Linear Rail alignment helper

This can be used to help align the linear rails

  * https://www.thingiverse.com/thing:2368837

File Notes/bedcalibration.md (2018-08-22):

# Duet Board Bed Leveling

With the duet board there are two forms of leveling

  * G30 - Tries to calculate the bed tilt / other parameters to compensate
  * G29 - Uses a grid of points for more traditional bed leveling for uneven beds

## Checking the Probe Offset

First its best to reduce the Feed / Travel speed of the probe in case something unexpected happens
This is the F and T parameters of the M558 command

```
M558 P4 R0.4 H3 F300 T300 I1
```

In order to check the probe offset

  * Attach the Probe
  * Home the machine
  * issue the command "M208 S1 Z-3"
    This should allow the head to travel down further than 0 by 3mm
  * Issue the command "G30"
    This will probe the center of the bed and set the 0 point based on the probe height.

  * Remove the Probe
  * Put a piece of paper under the nozzel
  * Gradually move the head down untill it's just above gripping the paper
  * Make a note of the Z value

In theory the Z value at this stage should be 0.1, if it isn't then we need to alter the Z Probe offset
The Z Probe offset is set via G31

```
G31 P100 X0 Y0 Z16.2
```

Note its also possible to use:
G30 S-1 to probe, then read off the Z height.

## Automated Leveling / G32

By issuing the **G32** command, or selecting **Auto Delta Calibration** on the main menu
this will trigger the commands within bed.g to be run
so G32 can be thought of as a overall do the bed leveling without specifying any parameters
with all the parameters being within the **bed.g** file such as Homing / G30 commands / G29 commands

### G30 Bed Leveling

Unlike traditional bed leveling, G30 attepts to work out calibration issues of the printer
such as

  * tilt of the bed
  * different heights of the end stops
  * angle of the towers

The way I do this within **bed.g**

  * Home the machine
  * move the ged down to about 120mm
  * run a single G30 command (no parameters) over the center to set the height of the machine (sets Z = 0 based on the probe height)
  * run a series of G30 commands to probe the bed
  * run G30 P16 X0 Y0 H0 Z-99999 S7

The default in the configuration is 7 factor leveling for the last line.
I've upped this to 9 factor to see how this works

#### Saving G30 Settings

We can save the settings for the G30 Bed leveling by using **M500**
This will save the settings to a file called **config-overide.g**
Note in order for these to be used, there needs to be a M501 command at the bottom of **config.g**

Typically these will show up under M665 which is the delta parameters.
And M666 which is end stop position corrections / tilt corrections.
Normally these are set to an approximate best guess value within config.g, but are then overriden by these values
within **config-override.g** which is from the automated calibration.

Typically for 7 factor calibration
```
M665 L272.251 R134.654 H295.189 B116.0 X0.238 Y0.543 Z0.000
M666 X-0.487 Y0.170 Z0.317 A0.00 B0.00
```

### G29 Bed Leveling

  * https://duet3d.dozuki.com/Wiki/Using_mesh_bed_compensation

G29 Bed leveling is the more traditional form of leveling.
This probes multiple points on the bed in the form of a grid and generates a heat map
which can be seen within the GUI

The G30 commands will always wipe out the G29 bed leveling information in memory
so if using G29 it should be done after G30 has been run

When running G29 on it's own with no parameters it should automatically save the results to
/sys/heightmap.csv

   * G29 S0 - run and save (default)
   * G29 S1 - load from file and activate
   * G29 S2 - clear bed height map
   * M561 - turn off bed compensation

The P option can be used with S0 or S1 to specify a different file

set 16.8
measured +0.3

set 17.1
measured +0.7

set 16.6
measured +0.1

## Delta Height

Hi,
Theres a couple of things I've spotted recently
This is to do with the calibration of a delta printer and perhaps some changes to the default config files

I'm using an Anycubic Kossel Linear Plus, Duet Wifi, latest firmware 2.01
The printer has a magnetic probe that clips directly underneath the nozzel at around 16.6mm dowards on the Z axis

the config files I'm using can be seen here
  * https://github.com/grbd/GBD.3DPrinter.Kossel.Anycubic/tree/master/DuetBoard/Config/configv2

## Delta Height

The first thing I've spotted which is quite important relates to the delta height
It might ether be a case of an error in my G-Code, or possibly a software bug, or maybe a missing feature I'm not sure
But I think the G30 autocalibration doesn't set the overall delta height automatically in relation to the end stops
Then again perhaps it's not designed to do that.

  * https://duet3d.dozuki.com/Wiki/Calibrating_a_delta_printer#Section_M665_command

This seems to suggest that you should get the delta height within 5mm of the bed before starting the calibration
so perhaps this is where I was going wrong

First as a starting point I used the following to setup the delta parameters
```
M665 R134.4 L271.5 B116 H300
M666 X0 Y0 Z0
```
Now the delta height is actually around 289.877 instead of 300 for info
If I run the auto-calibration / G32, then the end result will look something like
```
Diagonal 272.463, delta radius 134.676, homed height 299.998, bed radius 116.0, X 0.652°, Y 0.751°, Z 0.000°
```
This is still close to 300mm the original value
I think it's adjusting it based on the tilt of the bed etc, but not in relation to the end stops
It's not a big deal but I think it could catch someone out.

The way I get around this currently is to

  * Home machine
  * Attach the probe
  * heat the bed to aroung 60 degrees (just my own preference ro compensate for thermal expansion of the bed)
  * issue G30 S-1
  * repeat the home / G30 S-1 a couple of times to get a couple of values in the G-Code Log

  * raise the head by about 5mm, so the probe isn't touching the bed anymore
  * read the offset value in the G-Code logs, which in my case is **26.723**
  * Since I know the z probe offset is 16.6 (via a paper test I've done before)
    26.723 - 16.6 = 10.123 difference
  * so 300 - 10.123 = 289.877 as the new delta height

  * Lets set the new height with M665 H289.877
  * Next re-home the machine
  * Run delta-autocalibration
  * run "M500" to store the new settings into config-override.g

At this point if I home the machine then bring it down and do the paper test, it's spot on.
Unless this is supposed to be part of the existing G30 calibration
perhaps this should be automated via a new option for G30?
so instead of setting Z0, setting the delta height in relation to the end stops via a single probe to the center of the bed

## Auto Home

I've tweaked is the g-code within deltahome.g
https://github.com/grbd/GBD.3DPrinter.Kossel.Anycubic/blob/master/DuetBoard/Config/configv2/homedelta.g

This is a little less agressive and give more repeatable results when probing the bed with G30 S-1 after a homing cycle
compared to the the one from the configurator

## G30 / bed.g

For bed.g I used the configurator
However I needed to add a single **G30** to the beginning of the file
https://github.com/grbd/GBD.3DPrinter.Kossel.Anycubic/blob/master/DuetBoard/Config/configv2/bed.g

to set the Z0 correctly
otherwise it resulted in the probe crashing into the bed
this might have been due to the delta height being incorrect at the time I'm not sure
but it might be an idea to add it into the config generated by the configurator as a safety margin.

## Setting the initial delta height

1. set dive height to 100mm
M558 P4 R0.4 H100 F300 T3000

2. set defaults for delta calibration
M665 R134.4 L271.5 B116 H300
M666 X0 Y0 Z0

3. home device
4. run auto calibration
5. run M500 to store results

6. set dive height to 5mm
M558 P4 R0.4 H5 F300 T3000
7. re-run auto calibration

## Intial Probe calibration

1. home device
2. auto calibration
3. home device
4. move down 120
G1 Z120
5. allow travel below 0
M208 S1 Z-3

6. do a paper test
move slowly downwards to get offset

7. adjust delta height based on offset

current - works okay
M665 H290.024

## Calibration with G29 / Heated bed

next enable the heated bed lines
and G29 lines
re-run auto calibration
M500

## Tweaking height based on print

1. make a note of the existing delta height
M665
289.955

2. start a print of a long object
3. if it doest grip on the bed try increasing the delta height by 0.05mm at a time
using baby stepping
to get a final height
M665

-0.15mm is best - 290.105

## final probe adjust

we now know that our ideal delta height is 290.105
so we want that to show up after an autocalibration

1. adjust the G31 Z offset by small amounts
2. run auto calibration
3. check with M665 the new delta height
4. rinse and repeat untill the new delta height matches the known ideal

original is 16.6
G31 P100 X0 Y0 Z16.6

new
G31 P100 X0 Y0 Z16.695

todo
adding blu-tack to the inside of the probe helps prevent wobble
also set the A parameter to 10 for times to probe

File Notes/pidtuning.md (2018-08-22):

PID tuning bed

run the tuning
M303 H0 P1 S80

store settings to config-overide.g where we can copy them out
M500

show the tuning values
M303 H0

set tuning values in config.g
M307 H1 A188.4, C121.7, D1.4 S0.5

PID tunning hotend

run the tuning
M303 H1 P0.5 S230

store settings to config-overide.g where we can copy them out
M500

show the tuning values
M303 H1

set tuning values in config.g
M307 H1 A188.4, C121.7, D1.4 S0.5

Adjust the P setting (PWM) so that its as high as possible, but at the same time not too high
to high and it will overshoot / be overpowered
to low and it will take a long time to heat up

P0.5 has problems reaching 230 degrees
P0.6 seems to be a good value for mine

to prevent oscilation, try increasing the dead time
https://forum.duet3d.com/topic/5778/e3dv6-tuning/3

D6 seems like a good value

this seems to work best
M307 H1 A253.8 C118.5 D6 S0.50 V12.0 B0

results:

M303 H1 P1 S200
Auto tune phase 3, peak temperature was 204.7
Warning: Heater 1 appears to be over-powered. If left on at full power, its temperature is predicted to reach 470C.

M303 H1 P0.5 S230
Auto tune phase 3, peak temperature was 200.8

M303 H1 P0.6 S230
Auto tune phase 3, peak temperature was 201.6
Auto tune phase 3, peak temperature was 231.2

M307 H1 A255.6 C120.9 D6 S0.50 V12.0 B0

200.3 199.4
200.2 199.6

M307 H1 A253.8 C118.5 D1.6 S0.60 V12.0 B0

198.3 200.5

the results are different while printing
influenced by speed of printing and if the part fan is on
add a note about putting the part fan on before running the pid calibration

0.55 pmw seems okay but dips a bit during printing 
M303 H1 P0.55 S230

0.9 seems to be okay without warnings
M303 H1 P0.9 S190

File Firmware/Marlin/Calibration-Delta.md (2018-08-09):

# Delta Calibration

Next we're going to run delta auto calibration
this will use the probe 

  * https://hennerley.wordpress.com/2018/01/29/g29-vs-g33/
  * https://www.youtube.com/watch?v=U20_2BkuD4g
  * https://github.com/FLSun3dp/FLSun-Kossel-Mini/wiki/07.-G33-Auto-Calibration
  * http://marlinfw.org/docs/gcode/G033.html
  * https://www.thingiverse.com/thing:2256557

G29 is the traditional auto bed level which is sort of a fudge factor for unlevel beds
it can also compensate for non-calibrated delta machines
however using that can add overhead to the calculations needed on the board

it's best instead to use G33 to do delta calibration first
this works out the subtle differences in the angles of the towers and other parameters
assuming the bed is actually flat / level.

G29 can then be used after the calibration if the bed is uneven for any reason.
Note the Z Probe Offset (distance between the nozzel and probe switch)
doesn't need to be accurate for G33 to work so that can be done afterwards, but it may be need to be done before G29

## Testing the probe sensor

One thing we can do is test the probe sensor
by running the M119 command
then looking for the z_min

it should be listed as open for when the switch is not triggered, and TRIGGERED for when it's pushed in

## Running the initial delta calibration

We can see the current delta calibration settings under

  * Prepare -> Delta Calibration -> Delta Settings

The DiagRod setting is the length of the rod from the tower to the effector
so this won't change automatically.

Next we run the autocalibration (from ether the LCD menu or via G-Code)

  * Prepare -> Delta Calibration -> Auto Calibration <br>
    GCode G33
  * Prepare -> Delta Calibration -> Set Delta Height <br>
    GCode G33 P1

This should set

  * Height
  * EndStop measurements: Ex, Ey, Ez
  * Radius
  * Tower Angles: Tx, Ty, Tz

### Adjust end stop screws

Ideally we should try to get the E values all zero if possible or all the same
this can be done by adjusting the end stop screws

Example: mine after calibation

Calibration OK
Height:291.86
Ex:-1.24
Ey:-3.91
Ez:+0.00
Radius:134.32
Tx:-0.14
Ty:+0.17
Tz:-0.03
Save with M500 and/or copy to Configuration.h

### Store Settings

Finally we can store the settings via

  * Delta Calibration -> Store Settings

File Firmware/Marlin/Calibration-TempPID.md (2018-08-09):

# Temperature PID Calibration

This covers the calibration of the HotEnd / Bed using PID

## PID Hotend

To fine tune the PID settings for the heater you need to run
```
M106 S255
M303 E0 C10 S200
```
This should work out a set of values to use in terms of 
what kind of signals / how fast to heat the heater block etc

The defaults in the config are from my own printer
```
#define  DEFAULT_Kp 37.56
#define  DEFAULT_Ki 3.99
#define  DEFAULT_Kd 88.47
```

## PID Heated Bed

To fine tune the PID settings for the heatbed you need to run
```
M303 E-1 C10 S90
```
Note I had to run this more than once, since it timed out the first time
due to the bed taking so long to heat

The defaults in the config are from my own printer
```
#define  DEFAULT_bedKp 785.35
#define  DEFAULT_bedKi 154.79
#define  DEFAULT_bedKd 996.11
```

## Store Settings

At this point you can ether alter the Configuration.h and re-upload a new firmware
or do a Store Settings to store the changed settings to EEPROM instead

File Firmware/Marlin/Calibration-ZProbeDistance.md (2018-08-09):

# Z Probe Offset Calibration

The Z Probe Offset setting represents the distance difference between the end of the nozzel and the Probe Switch
Normally the probe should have a fixed distance for the V1 for example it's usually 19.00mm

However if the nozzel has been replaced or is slightly higher or lower
or if the probe is slighlty off then it can be useful to calibrate this setting manually as well.

## The paper method

The paper method which is quite common involves the following to determine the Z offset

  * Make sure the probe is not fitted.
  * Put a sheet of paper on the bed
  * Measure paper thickness with calipers
  * Prepare -> Move Axis -> Move Z
  * Move the Z down until the paper is just resisting
    (for example scratchy at 1.7, stuck at 1.8, space at 1.6, z offset used of -1.65)

## The electrical method

TODO

## Set the Z Offset

The first place to store the Z offset is

  * Control -> Motion -> Z Offset

Next we need to re-set the Delta Height
we can ether manually remove the offset from the Height in the Delta Calibration settings
or run with the probe attached

  * Prepare -> Delta Calibration -> Set Delta Height <br>
    GCode G33 P1

For example if the existing Z Offset was -14.9 <br>
-14.9 + -1.65 = -16.55

The idea is that when the z axis is at 0 the paper should be just about catching.

## Store Settings

  * TODO
  * Delta Calibration -> Store Settings

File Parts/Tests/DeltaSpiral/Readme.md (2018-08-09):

# Readme

  * https://www.thingiverse.com/thing:2764984/files

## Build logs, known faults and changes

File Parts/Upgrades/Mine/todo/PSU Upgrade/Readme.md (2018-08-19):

# Readme

  * https://www.amazon.co.uk/EVGA-WHITE-Power-Supply-100-W1-0600-K3/dp/B01127D0MY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

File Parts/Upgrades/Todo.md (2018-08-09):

# TODO

## TODO

### Driver Cooling

Look at moving the driver into its own box with a PCI slot cooler

  * https://www.thingiverse.com/thing:2990467
  * https://www.thingiverse.com/thing:2847057
  * https://www.thingiverse.com/thing:2551172
  * https://www.thingiverse.com/thing:2516507

### Inductive end stops

Look at changing the end stops with inductive ones

### Part Collection

check these out

  * https://www.thingiverse.com/thing:2971288
  * https://www.thingiverse.com/thing:2889662

### Top Plates

  * https://www.thingiverse.com/thing:1969059

### Bottom Corner Plates

  * https://www.thingiverse.com/thing:2478566 - check auto leveling
  * https://www.thingiverse.com/thing:2961934
  * https://www.thingiverse.com/thing:2945910
  * https://www.thingiverse.com/thing:2918735
  * https://www.thingiverse.com/thing:2883793
  * https://www.thingiverse.com/thing:2867535
  * https://www.thingiverse.com/thing:2831633 - hardned corner
  * https://www.thingiverse.com/thing:2772243
  * https://www.thingiverse.com/thing:2771991
  * https://www.thingiverse.com/thing:2764353
  * https://www.thingiverse.com/thing:2620272 - re-enforcement

### Bed Clips

  * https://www.thingiverse.com/thing:2880708
  * https://www.thingiverse.com/thing:2843953
  * https://www.thingiverse.com/thing:2831022
  * https://www.thingiverse.com/thing:2578247
  * https://www.thingiverse.com/thing:2575623
  * https://www.thingiverse.com/thing:2443261

### Enclosure

  * https://www.thingiverse.com/thing:2943798
  * https://www.thingiverse.com/thing:2829057
  * https://www.thingiverse.com/thing:2782949
  * https://www.thingiverse.com/thing:2626291
  * https://www.thingiverse.com/thing:2577313

### Anchoring

Try using this to anchor to the bench

  * https://www.thingiverse.com/thing:2941886/comments

### Upper part Cooling Fan

Look into

  * https://www.thingiverse.com/thing:2908841
  * https://www.thingiverse.com/thing:2735314

### Rubbish Bin

  * https://www.thingiverse.com/thing:2900095

### Magnet Arms

  * https://www.thingiverse.com/thing:2859992
  * https://www.thingiverse.com/thing:2842176

### Arm spring dampening

  * https://www.thingiverse.com/thing:2764301
  * https://www.thingiverse.com/thing:2764110

### Filament runout detection

  * https://www.thingiverse.com/thing:2764075

### Led lighting

  * https://www.thingiverse.com/thing:2848456
  * https://www.thingiverse.com/thing:2732105
  * https://www.thingiverse.com/thing:2578625
  * https://www.thingiverse.com/thing:2544594
  * https://www.thingiverse.com/thing:2134894

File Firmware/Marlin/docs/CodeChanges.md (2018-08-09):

# Notes

## Configuration Notes

### Motherboard setting

  * original mother board setting was BOARD_RAMPS_13_EFB -> 33 in boards.h
  * this is checked in pins.h - MB(RAMPS_13_EFB)
  * this sets IS_RAMPS_EFB
  * then includes pins_RAMPS_13.h which defines IS_RAMPS_13

  * new mother board setting is BOARD_TRIGORILLA -> 343 in boards.h
  * this is checked in pins.h - MB(TRIGORILLA)
  * then includes pins_TRIGORILLA.h
  * IS_RAMPS_EFB is set here instead
  * pins_RAMPS_13.h is then included which defines IS_RAMPS_13

### Fan fix

It looks like there was some code in originally to turn on the fan for the coldend when it got over 60 degrees
a sort of workaround for this
https://github.com/MarlinFirmware/Marlin/issues/3234

I think that code is no longer needed if we use the following in config_adv

#define E0_AUTO_FAN_PIN 44 <- we dont need to set this as it's captured within pins_TRIGORILLA.h via ORIG_E0_AUTO_FAN_PIN
#define E1_AUTO_FAN_PIN -1
#define E2_AUTO_FAN_PIN -1
#define E3_AUTO_FAN_PIN -1
#define E4_AUTO_FAN_PIN -1
#define EXTRUDER_AUTO_FAN_TEMPERATURE 60
#define EXTRUDER_AUTO_FAN_SPEED   255  // == full speed

also within pins_TRIGORILLA.h I've commented out the code that sets FAN_PIN to 44
as that should be left at pin 9 for the part fan

### endstops

I dont think the below is needed - in pins_RAMPS_OLD.h
the pins are never used, but are available

 //
 // Limit Switches
 //
-#define X_MIN_PIN           3
+#define X_MIN_PIN           -1
 #define X_MAX_PIN           2
-#define Y_MIN_PIN          16
+#define Y_MIN_PIN          -1
 #define Y_MAX_PIN          17
 #define Z_MIN_PIN          18
 #define Z_MAX_PIN          19

### Probe

For Version 1 I think it's
#define X_PROBE_OFFSET_FROM_EXTRUDER 0     // X offset: -left  +right  [of the nozzle]
#define Y_PROBE_OFFSET_FROM_EXTRUDER 0     // Y offset: -front +behind [the nozzle]
#define Z_PROBE_OFFSET_FROM_EXTRUDER -19.0   // Z offset: -below +above  [the nozzle], Anycubic Leveling Module v1:-19.0, v2:-14.9

For version 2 it's
#define X_PROBE_OFFSET_FROM_EXTRUDER 0     // X offset: -left  +right  [of the nozzle]
#define Y_PROBE_OFFSET_FROM_EXTRUDER 0     // Y offset: -front +behind [the nozzle]
#define Z_PROBE_OFFSET_FROM_EXTRUDER -14.9   // Z offset: -below +above  [the nozzle], Anycubic Leveling Module v1:-18.0, v2:-14.9

### Code patch

It looks like theres an issue for delta printers
if DELTA is enabled
but the following is not set within Configuration.h MIN_SOFTWARE_ENDSTOPS MAX_SOFTWARE_ENDSTOPS
then HAS_SOFTWARE_ENDSTOPS is never set

this leads to the following not being declared
  float soft_endstop_radius, soft_endstop_radius_2;

this creates a problem when compiling the update_software_endstops function

simple fix is to use

#if IS_KINEMATIC
  float soft_endstop_radius, soft_endstop_radius_2;
#endif
#if HAS_SOFTWARE_ENDSTOPS
  bool soft_endstops_enabled = true;
#endif

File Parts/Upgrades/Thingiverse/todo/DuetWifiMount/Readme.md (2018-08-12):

# Readme

Original design from

  * https://www.thingiverse.com/thing:2894696/files

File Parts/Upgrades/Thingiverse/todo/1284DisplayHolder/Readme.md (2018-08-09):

# Readme

  * https://www.thingiverse.com/thing:1676899
  * https://www.thingiverse.com/thing:27960337

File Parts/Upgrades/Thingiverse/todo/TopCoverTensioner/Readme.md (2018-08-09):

# Readme

  * https://www.thingiverse.com/thing:2827665/files

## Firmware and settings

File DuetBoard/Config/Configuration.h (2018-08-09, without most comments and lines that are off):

#define CONFIGURATION_H
#define CONFIGURATION_H_VERSION 010109
#define STRING_CONFIG_H_AUTHOR "(none, default config)" // Who made the changes.
#define SHOW_BOOTSCREEN
#define STRING_SPLASH_LINE1 SHORT_BUILD_VERSION // will be shown during bootup in line 1
#define STRING_SPLASH_LINE2 "Welcome to Anycubic." // will be shown during bootup in line 2
#define SERIAL_PORT 0
#define BAUDRATE 250000
  #define MOTHERBOARD BOARD_TRIGORILLA_13
#define CUSTOM_MACHINE_NAME "Anycubic Kossel"
#define EXTRUDERS 1
#define DEFAULT_NOMINAL_FILAMENT_DIA 1.75
#define POWER_SUPPLY 1
#define TEMP_SENSOR_0 5
#define TEMP_SENSOR_1 0
#define TEMP_SENSOR_2 0
#define TEMP_SENSOR_3 0
#define TEMP_SENSOR_4 0
#define TEMP_SENSOR_BED 5
#define TEMP_SENSOR_CHAMBER 0
#define DUMMY_THERMISTOR_998_VALUE 25
#define DUMMY_THERMISTOR_999_VALUE 100
#define MAX_REDUNDANT_TEMP_SENSOR_DIFF 5
#define TEMP_RESIDENCY_TIME 10  // (seconds)
#define TEMP_HYSTERESIS 3       // (degC) range of +/- temperatures considered "close" to the target one
#define TEMP_WINDOW     1       // (degC) Window around target to start the residency timer x degC early.
#define TEMP_BED_RESIDENCY_TIME 0   // (seconds)
#define TEMP_BED_HYSTERESIS 3       // (degC) range of +/- temperatures considered "close" to the target one
#define TEMP_BED_WINDOW     1       // (degC) Window around target to start the residency timer x degC early.
#define HEATER_0_MINTEMP 5
#define HEATER_1_MINTEMP 5
#define HEATER_2_MINTEMP 5
#define HEATER_3_MINTEMP 5
#define HEATER_4_MINTEMP 5
#define BED_MINTEMP 5
#define HEATER_0_MAXTEMP 275
#define HEATER_1_MAXTEMP 275
#define HEATER_2_MAXTEMP 275
#define HEATER_3_MAXTEMP 275
#define HEATER_4_MAXTEMP 275
#define BED_MAXTEMP 120
#define PIDTEMP
#define BANG_MAX 255     // Limits current to nozzle while in bang-bang mode; 255=full current
#define PID_MAX BANG_MAX // Limits current to nozzle while PID is active (see PID_FUNCTIONAL_RANGE below); 255=full current
#define PID_K1 0.95      // Smoothing factor within any PID loop
  #define PID_FUNCTIONAL_RANGE 10 // If the temperature difference between the target temperature and the actual temperature
  #define  DEFAULT_Kp 37.56
  #define  DEFAULT_Ki 3.99
  #define  DEFAULT_Kd 88.47
#define PIDTEMPBED
#define MAX_BED_POWER 255 // limits duty cycle to bed; 255=full current
  #define  DEFAULT_bedKp 785.35
  #define  DEFAULT_bedKi 154.79
  #define  DEFAULT_bedKd 996.11
#define PREVENT_COLD_EXTRUSION
#define EXTRUDE_MINTEMP 170
#define PREVENT_LENGTHY_EXTRUDE
#define EXTRUDE_MAXLENGTH 200
#define THERMAL_PROTECTION_HOTENDS // Enable thermal protection for all extruders
#define THERMAL_PROTECTION_BED     // Enable thermal protection for the heated bed
#define DELTA
  #define DELTA_SEGMENTS_PER_SECOND 200
  #define DELTA_FEEDRATE_SCALING
  #define DELTA_AUTO_CALIBRATION
    #define DELTA_CALIBRATION_DEFAULT_POINTS 10
    #define DELTA_CALIBRATION_RADIUS 110.0 // mm
    #define PROBE_MANUALLY_STEP 0.05 // mm
  #define DELTA_ENDSTOP_ADJ { 0.0, 0.0, 0.0 } // get these from auto calibrate
  #define DELTA_TOWER_ANGLE_TRIM { 0.0, 0.0, 0.0 } // get these values from auto calibrate
#define USE_ZMIN_PLUG // a Z probe
#define USE_XMAX_PLUG
#define USE_YMAX_PLUG
#define USE_ZMAX_PLUG
#define ENDSTOPPULLUPS
#define X_MIN_ENDSTOP_INVERTING false  // set to true to invert the logic of the endstop.
#define Y_MIN_ENDSTOP_INVERTING false  // set to true to invert the logic of the endstop.
#define Z_MIN_ENDSTOP_INVERTING false  // set to true to invert the logic of the endstop.
#define X_MAX_ENDSTOP_INVERTING false  // set to true to invert the logic of the endstop.
#define Y_MAX_ENDSTOP_INVERTING false  // set to true to invert the logic of the endstop.
#define Z_MAX_ENDSTOP_INVERTING false  // set to true to invert the logic of the endstop.
#define Z_MIN_PROBE_ENDSTOP_INVERTING false  // set to true to invert the logic of the probe.
#define DEFAULT_MAX_FEEDRATE          { 200, 200, 200, 50 }
#define DEFAULT_MAX_ACCELERATION      { 3000, 3000, 3000, 3000 }
#define DEFAULT_ACCELERATION          2000    // X, Y, Z and E acceleration for printing moves
#define DEFAULT_RETRACT_ACCELERATION  2000    // E acceleration for retracts
#define DEFAULT_TRAVEL_ACCELERATION   2000    // X, Y, Z acceleration for travel (non printing) moves
#define DEFAULT_XJERK                  5.0
#define DEFAULT_YJERK                 DEFAULT_XJERK
#define DEFAULT_ZJERK                 DEFAULT_XJERK // Must be same as XY for delta
#define DEFAULT_EJERK                  5.0
#define Z_MIN_PROBE_USES_Z_MIN_ENDSTOP_PIN
#define FIX_MOUNTED_PROBE
#define X_PROBE_OFFSET_FROM_EXTRUDER 0     // X offset: -left  +right  [of the nozzle]
#define Y_PROBE_OFFSET_FROM_EXTRUDER 0     // Y offset: -front +behind [the nozzle]
#define Z_PROBE_OFFSET_FROM_EXTRUDER -16.8 // Z offset: -below +above  [the nozzle], Anycubic Leveling Module v1:-19.0, v2:-16.8
#define MIN_PROBE_EDGE 10
#define XY_PROBE_SPEED 4000
#define Z_PROBE_SPEED_FAST HOMING_FEEDRATE_Z
#define Z_PROBE_SPEED_SLOW (Z_PROBE_SPEED_FAST / 3)
#define Z_CLEARANCE_DEPLOY_PROBE   50 // Z Clearance for Deploy/Stow
#define Z_CLEARANCE_BETWEEN_PROBES  5 // Z Clearance between probe points
#define Z_CLEARANCE_MULTI_PROBE     5 // Z Clearance between multiple probes
#define Z_PROBE_LOW_POINT          -2 // Farthest distance below the trigger-point to go before stopping
#define Z_PROBE_OFFSET_RANGE_MIN -20
#define Z_PROBE_OFFSET_RANGE_MAX 20
#define X_ENABLE_ON 0
#define Y_ENABLE_ON 0
#define Z_ENABLE_ON 0
#define E_ENABLE_ON 0 // For all extruders
#define DISABLE_X false
#define DISABLE_Y false
#define DISABLE_Z false
#define DISABLE_E false // For all extruders
#define DISABLE_INACTIVE_EXTRUDER true // Keep only the active extruder enabled.
#define INVERT_X_DIR true // DELTA does not invert
#define INVERT_Y_DIR true
#define INVERT_Z_DIR true
#define INVERT_E0_DIR true  // For TMC2100 set to false
#define INVERT_E1_DIR false
#define INVERT_E2_DIR false
#define INVERT_E3_DIR false
#define INVERT_E4_DIR false
#define NO_MOTION_BEFORE_HOMING  // Inhibit movement until all axes have been homed
#define X_HOME_DIR 1  // deltas always home to max
#define Y_HOME_DIR 1
#define Z_HOME_DIR 1
#define X_BED_SIZE ((DELTA_PRINTABLE_RADIUS) * 2)
#define Y_BED_SIZE ((DELTA_PRINTABLE_RADIUS) * 2)
#define X_MIN_POS -(DELTA_PRINTABLE_RADIUS)
#define Y_MIN_POS -(DELTA_PRINTABLE_RADIUS)
#define Z_MIN_POS 0
#define X_MAX_POS DELTA_PRINTABLE_RADIUS
#define Y_MAX_POS DELTA_PRINTABLE_RADIUS
#define Z_MAX_POS MANUAL_Z_HOME_POS
#define AUTO_BED_LEVELING_BILINEAR
#define RESTORE_LEVELING_AFTER_G28
  #define SEGMENT_LEVELED_MOVES
  #define LEVELED_SEGMENT_LENGTH 5.0 // (mm) Length of all segments (except the last one)
  #define GRID_MAX_POINTS_X 9
  #define GRID_MAX_POINTS_Y GRID_MAX_POINTS_X
  #define LEFT_PROBE_BED_POSITION -(DELTA_PRINTABLE_RADIUS -(MIN_PROBE_EDGE))
  #define RIGHT_PROBE_BED_POSITION DELTA_PRINTABLE_RADIUS -(MIN_PROBE_EDGE)
  #define FRONT_PROBE_BED_POSITION -(DELTA_PRINTABLE_RADIUS -(MIN_PROBE_EDGE))
  #define BACK_PROBE_BED_POSITION DELTA_PRINTABLE_RADIUS -(MIN_PROBE_EDGE)
#define BED_CENTER_AT_0_0
#define MANUAL_Z_HOME_POS DELTA_HEIGHT // Distance between the nozzle to printbed after homing
#define Z_SAFE_HOMING
  #define Z_SAFE_HOMING_X_POINT ((X_BED_SIZE) / 2)    // X point for Z homing when homing all axes (G28).
  #define Z_SAFE_HOMING_Y_POINT ((Y_BED_SIZE) / 2)    // Y point for Z homing when homing all axes (G28).
#define HOMING_FEEDRATE_Z  (50*60)
#define EEPROM_SETTINGS // Enable for M500 and M501 commands
#define EEPROM_CHITCHAT   // Give feedback on EEPROM commands. Disable to save PROGMEM.
#define HOST_KEEPALIVE_FEATURE        // Disable this if your host doesn't like keepalive messages
#define DEFAULT_KEEPALIVE_INTERVAL 2  // Number of seconds between "busy" messages. Set with M113.
#define BUSY_WHILE_HEATING            // Some hosts require "busy" messages even during heating
#define PREHEAT_1_TEMP_HOTEND 180
#define PREHEAT_1_TEMP_BED     70
#define PREHEAT_1_FAN_SPEED   255 // Value from 0 to 255
#define PREHEAT_2_TEMP_HOTEND 240
#define PREHEAT_2_TEMP_BED    80
#define PREHEAT_2_FAN_SPEED   255 // Value from 0 to 255
#define NOZZLE_PARK_FEATURE
  #define NOZZLE_PARK_POINT { (X_MIN_POS + 10), 0, 30 }
  #define NOZZLE_PARK_XY_FEEDRATE 100   // X and Y axes feedrate in mm/s (also used for delta printers Z axis)
  #define NOZZLE_PARK_Z_FEEDRATE 100    // Z axis feedrate in mm/s (not used for delta printers)
#define PRINTJOB_TIMER_AUTOSTART
#define PRINTCOUNTER
#define LCD_LANGUAGE en
#define DISPLAY_CHARSET_HD44780 JAPANESE
#define SDSUPPORT
#define SPI_SPEED SPI_QUARTER_SPEED
#define SD_CHECK_AND_RETRY
#define REPRAP_DISCOUNT_SMART_CONTROLLER
#define ULTRA_LCD
#define SOFT_PWM_SCALE 0
#define SERVO_DELAY { 300 }

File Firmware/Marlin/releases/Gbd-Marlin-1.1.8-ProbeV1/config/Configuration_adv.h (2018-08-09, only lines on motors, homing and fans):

  #define CONTROLLER_FAN_PIN 7           // Set a custom pin for the controller fan
#define E0_AUTO_FAN_PIN 44
#define E1_AUTO_FAN_PIN -1
#define E2_AUTO_FAN_PIN -1
#define E3_AUTO_FAN_PIN -1
#define E4_AUTO_FAN_PIN -1
#define X_HOME_BUMP_MM 5
#define Y_HOME_BUMP_MM 5
#define Z_HOME_BUMP_MM 5 // deltas need the same for all three axis
#define HOMING_BUMP_DIVISOR {10, 10, 10}  // Re-Bump Speed Divisor (Divides the Homing Feedrate)
#define MICROSTEP_MODES {16,16,16,16,16} // [1,2,4,8,16]
#define DIGIPOT_I2C_MOTOR_CURRENTS { 1.0, 1.0, 1.0, 1.0, 1.0, 1.0, 1.0, 1.0 }  //  AZTEEG_X3_PRO
#define ADVANCED_PAUSE_FEATURE
  #define ADVANCED_PAUSE_EXTRUDE_FEEDRATE 3   // Extrude filament feedrate in mm/s - must be slower than load feedrate
  #define ADVANCED_PAUSE_EXTRUDE_LENGTH 30    // Extrude filament length in mm after filament is loaded over the hotend,

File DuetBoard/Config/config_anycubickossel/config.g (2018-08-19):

; Configuration file for Duet WiFi (firmware version 1.21)
; executed by the firmware on start-up

; General preferences
G21                                                  ; Work in millimetres
G90                                                  ; Send absolute coordinates...
M83                                                  ; ...but relative extruder moves

;*** The homed height is deliberately set too high in the following - you will adjust it during calibration.
M665 R134.4 L271.5 B116 H300                       ; Set delta radius, diagonal rod length, printable radius and homed height
M666 X0 Y0 Z0                                        ; Put your endstop adjustments here, or let auto calibration find them

; Network
M111 S0                                              ; Debug off
M550 PAnycubic1                                      ; Set machine name
M587 S"************" P"**************"               ; Configure access point.
M552 S1                                              ; Enable network
M586 P0 S1                                           ; Enable HTTP
M586 P1 S0                                           ; Disable FTP
M586 P2 S0                                           ; Disable Telnet
M555 P2	                                             ; Set output to look like Marlin

; Drives
M569 P0 S1                                           ; Drive 0 goes forwards
M569 P1 S1                                           ; Drive 1 goes forwards
M569 P2 S1                                           ; Drive 2 goes forwards
M569 P3 S1                                           ; Drive 3 goes forwards
M350 X16 Y16 Z16 E16 I1                              ; Configure microstepping with interpolation
M92 X80 Y80 Z80 E98.6                                ; Set steps per mm
M566 X300 Y300 Z300 E300                             ; Set maximum instantaneous speed changes (mm/min) / Jerk values
;M203 X12000 Y12000 Z12000 E3000                     ; Set maximum speeds 12000 (mm/min) / 200 (mm/sec) - Todo Optimum speeds
M203 X6000 Y6000 Z6000 E1000                         ; Set maximum speeds 12000 (mm/min) / 200 (mm/sec) - testing
;M203 X100 Y100 Z100 E100                         ; Set maximum speeds 12000 (mm/min) / 200 (mm/sec) - testing
M201 X2000 Y2000 Z2000 E2000                         ; Set accelerations (mm/s^2)
;M906 X1200 Y1200 Z1200 E1200 I30                    ; Set motor currents (mA) and motor idle factor in per cent
M906 X1000 Y1000 Z1000 E1000 I30                     ; Set motor currents (mA) and increase idle current to 30%
M84 S30                                              ; Set idle timeout

; Axis Limits
M208 Z0 S1                                           ; Set minimum Z

; Endstops
M574 X2 Y2 Z2 S1                                     ; Set active high endstops

; Probe v1 (broken) = 16.2, (good) = 19.0 (inverted)
; Probe v2 (good)   = 16.695

; Z-Probe
;M558 P4 R0.4 H3 F300 T3000 I1                         ; Use E0 end stop for probe - Probe V1
M558 P4 R0.4 H3 F300 T1000                            ; Use E0 end stop for probe - Probe V2

;G31 P100 X0 Y0 Z16.2                                 ; Set Z probe trigger value, offset and trigger height - Probe V1
G31 P100 X0 Y0 Z16.695                                ; Set Z probe trigger value, offset and trigger height - Probe V2
M557 R110 S20                                        ; Define mesh grid

; Heaters
M305 P0 T100000 B4267 C0 R4700                       ; Set thermistor + ADC parameters for heater 0
M143 H0 S120                                         ; Set temperature limit for heater 0 to 120C
M305 P1 T100000 B4267 C0 R4700                       ; Set thermistor + ADC parameters for heater 1
M143 H1 S275                                         ; Set temperature limit for heater 1 to 275C

; Heater Timeout
M570 S180                                            ; Hot end may be a little slow to heat up so allow it 180 seconds

; Fans
; Controller Fan hooked up to always on Fan
; 31Hz seems to generate less buzz during pwm
; Full on after 60 degrees
M106 P0 S0 I0 F31 H-1 B1 CPartFan1                   ; Used to cool the part
;M106 P1 S0 I0 F31 H-1                               ; Spare
M106 P2 S0 I0 F31 H1 L1 T60 CHotendFan1              ; Used to cool the hotend

; Tools
M563 P0 D0 H1                                        ; Define tool 0
G10 P0 X0 Y0 Z0                                      ; Set tool 0 axis offsets
G10 P0 R0 S0                                         ; Set initial tool 0 active and standby temperatures to 0C

; Automatic power saving
M911 S10 R11 P"M913 X0 Y0 G91 M83 G1 Z3 E-5 F1000"   ; Set voltage thresholds and actions to run on power loss

; Custom settings

; Miscellaneous
T0                                                   ; Select first tool


; Load settings from config-overide.g
; typically those auto calibrated
M501

; Load G29 bed leveling file
G29 S1

; Note with my current bed a ultrabase, the delta height should be around
; M665 H290.156
; within config-override after a auto calibration / M500 save

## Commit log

2018-08-09 home changes
    [homedelta.g]
2018-08-12 additional parts
    [20t_idler_pulley.SLDPRT, 20t_pulley.SLDPRT, AnycubicEffector.SLDPRT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]
2018-08-19 updated duet settings to now working
    [bed.g, cancel.g, config-override.g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]
2018-08-19 Added cura settings
    [Anycubic+Linear+Plus.global.cfg, fdmextruder+%232.extruder.cfg]
2018-08-19 upgrades cleanup
    [20t_idler_pulley.SLDPRT, 20t_pulley.SLDPRT, AnyCubic_Part_Fan_v3.stl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]
2018-08-22 added notes
    [20t_idler_pulley.SLDPRT, 20t_pulley.SLDPRT, ALP_duetwifi_mount_front.3mf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]
2018-08-23 updates to spool mount
    [Bearing.SLDPRT, M6 Bolt.SLDPRT, M6 Nut.SLDPRT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]

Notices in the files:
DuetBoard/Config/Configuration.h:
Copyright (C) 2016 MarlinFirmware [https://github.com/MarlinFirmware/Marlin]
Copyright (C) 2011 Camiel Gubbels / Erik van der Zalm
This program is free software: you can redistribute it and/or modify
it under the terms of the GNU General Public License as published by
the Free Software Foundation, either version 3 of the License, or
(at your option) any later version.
